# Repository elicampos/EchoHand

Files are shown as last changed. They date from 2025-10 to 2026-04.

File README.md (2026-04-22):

# EchoHand

A haptic feedback glove for VR applications utilizing ESP32-S3 microcontrollers. 

## Project Overview

EchoHand is a wearable haptic glove that captures hand and finger movements, and provides haptic feedback through the servo motors. The system communicates primary through WI-FI but also supports USB and Bluetooth Serial to transmit all the sensor data to the computer in real-time through the OpenGloves application.

## System Architecture

### External Interface

The external interface layer is executed primarily in `SerialCommunication.cpp` or `WifiCommuncation.cpp` and is responsible for receving and sending packets to the computer running the virtual reality enviornment.

- Configures Bluetooth Serial Communcation and has some variables to toggle AT mode for baudrates changes
- Configures ESP-NOW which allows the ESP32-S3 to talk to the computer quickly and asynchronously.
- Configures USB Serial by printing through default COM port

### DataBroker

Data storage is managed through `DataBroker.h`, which implements a singleton pattern for centralized state management. This component:

- Provides getters and setters for all sensor and actuator values
- Implements a snapshot mechanism with revision counters for consistent multi-field reads
- Stores current values for finger angles, servo positions, and button inputs

### Internal Systems

The internal processing layer handles data transformation and control logic. This component performs:

- **Sensor Mapping**: Get's center of raw ADC values (0-4095) to get more accurate values
- **Command Translation**: Translates serial commands PWM signals for servo motor control
- **State Updates**: Continuously updates the DataBroker with processed sensor data
- **Haptic Control**: Manages the relationship between virtual interactions and physical feedback through servo systems

### Information Handling

Data integrity is maintained through:
- Validation of sensor data ranges before processing
- Error checking on state updates to prevent corruption
- Verifying presence of the null terminator character in strings to prevent overflows
- Ensuring we never read outside of the bounds of C-style strings

### Communication

Communication is done through WI-FI, USB Serial, Bluetooth Serial and is dependent on the values in `config.h`.
- **Output Characteristic**: Transmits finger angle data and button values
- **Input Characteristic**: Receives haptic feedback commands for servos

### Integrity & Resilience

Current security and reliability features include:
- **RTOS Task Management**: FreeRTOS ensures deterministic behavior 

Future security and reliability features include:
- **Encryption**: All Bluetooth packets are encrypted(after pairing) to prevent man-in-the-middle attacks
- **Pairing Protocol**: Only authenticated devices can connect and exchange data

## Known Bugs

### 1. Random Finger position Jitter
**Description**: Due to no low-pass filter on the slider pins. Implementing this via software will cause too much of a delay.

## Future Work

#### 1. User-facing application for easy firmware changes
- **Description**: Create GUI software to allow users to send custom or pre-configured payloads to the EchoHand to update the current EchoHand settings during run-time.

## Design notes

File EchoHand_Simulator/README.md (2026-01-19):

# EchoHand Simulation Guide

## 1. Environment Setup

Make sure you are running this on a windows machine as this is a windows only application.

### ESP-IDF Extension (VSCode)
1.  **Install the Extension**: Search for "ESP-IDF" in the VSCode Extensions marketplace and install it.
2.  **Setup / Configuration**:
    *   Open the setup wizard (Command Palette: `ESP-IDF: Configure ESP-IDF extension`).
    *   **CRITICAL**: Select version **v5.3.4**. This version is strictly required for compatibility with the Arduino library used in this project.
    *   Follow the prompts to install tools.
3.  **Target Selection**:
    *   Set the target device to **esp32s3**.
    *   (Command Palette: `ESP-IDF: Set Espressif Device Target` -> `esp32s3`).

### Wokwi Simulator Extension (VSCode)
1.  **Install the Extension**: Search for "Wokwi for VSCode".
2.  **License**: You will need a valid license. Follow the extension's prompts to get a license from the Wokwi website and activate it.

---

## 2. Running the Firmware Simulation

1.  **Build Firmware**:
    *   Use the ESP-IDF extension icons (usually at the bottom bar) or Command Palette `ESP-IDF: Build your project` to compile the firmware.
2.  **Start Simulation**:
    *   Open the `diagram.json` file (or open the Wokwi GUI).
    *   Start the simulation.
    *   **Note**: The Wokwi simulation acts as the TCP Server. It must be running *before* you start the desktop visualizer.

> [!IMPORTANT]
> **Focus Issue**: If the data stream from Wokwi stops or lags, make sure you **click back into the VSCode window** showing the simulation. Browsers/Electron apps sometimes throttle background tabs/windows.

---

## 3. Running the Desktop Simulator

The desktop application visualizes the hand data received from the Wokwi simulation.

1.  **Navigate to Directory**:
    Open a terminal and navigate to the simulator folder:
    ```powershell
    cd EchoHand_Simulator
    ```

2.  **Build Application**:
    Run `make` to compile the C++ application (ensure you have MinGW/Make installed):
    ```powershell
    make
    ```

3.  **Run Application**:
    Execute the binary from the `bin` folder:
    ```powershell
    .\bin\opengloves_sim.exe
    ```

---

## 4. Controls & Interaction

Once both the Simulation (Server) and Desktop App (Client) are running:

*   **Modify Payload**:
    *   **Potentiometers**: Adjust these in the Wokwi view to simulate **Flex Sensors** (controlling finger curl).
    *   **Buttons**: Click to simulate Controller Buttons (A, B, Trigger, etc.).
    *   **Joystick**: Drag to simulate joystick movement.

*   **Desktop App Controls**:
    *   `W`, `A`, `S`, `D`: Move Camera
    *   `Right Click + Drag`: Look Around
    *   `P`: Toggle Protocol Reference Overlay

---

## Important Notes

*   **Launch Order**: ALWAYS run the **Wokwi Simulation first**, then the **OpenGloves Simulator**. The simulator tries to connect to localhost on launch; if the server isn't there, it will fail.
*   **Missing Payloads**: If you don't see the hand moving, check that Wokwi is actually sending data (monitor the serial output in VSCode) and that the VSCode window is focused.
*   **Future Features**: 
    *   Support for servo feedback (computer -> esp32).
    *   Reading commands from the computer.

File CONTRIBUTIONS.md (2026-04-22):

Name | Date | Start Time | End Time | Total Time (HH:MM) | Description of Work
--- | --- | --- | --- | --- | --- 
Anton Rushevich, Eli Campos, Gabriella Conde, Michael Knauf, Shawn Rhoads | 10/01/2025 | 12:00:00 PM | 12:00:00 PM | 0:00:00 | Work on Design Draft document. 
Eli Campos | 10/02/2025 | 99:99 PM | 99:99 PM | 0:00 | Work on Draft Schematic.
Eli Campos | 10/03/2025 | 99:99 PM | 99:99 PM | 0:00 | Work on Draft Schematic and High-Level System Diagram.
Eli Campos | 10/11/2025 | 99:99 PM | 99:99 PM | 0:00 | Work on sourcing and ordering parts.
Michael Knauf | 10/15/2025 | 7:27 PM | 8:09 PM | 0:40 | Work on Environmental Sustainability section for Design Plan revision, revising time sheet
Gabriella Conde | 10/18/2025 | 5:16 AM | 6:24 AM | 01:08 | Research and write repairability section of Design Draft.
Eli Campos | 10/19/2025 | 12:00 AM | 4:17 AM | 4:17 | Research and write risk section of Design Draft. 
Michael Knauf | 10/25/2025 | 8:05 PM | 10:00 PM | 1:55 | Set up Arduino environment and tested and showed that Bluetooth Serial failed
Eli Campos | 10/25/2025 | 12:30 PM | 6:00pm | 5:30 | Reading ESP32 Docuementation on the adc and pushed first RTOS main file.
Michael Knauf | 10/25/2025 | 1:12 PM | 10:15 PM | 9:03 | Making BLE Pre-alpha setup and debugging BLE integration
Gabriella Conde | 10/25/2025 | 2:36 PM | 6:25 PM | 3:49 | Drafting and prototyping of flex-sensor/esp32 circuit.
Shawn Rhoads | 10/26/2025 | 11:38 AM | 5:32 PM | 5:56 | Initial data store code and BLE integration
Eli Campos | 10/26/2025 | 3:00 PM | 12:00 AM | 9:00 | Finializing adc polling code, tweaking circuit and purchasing more components. 
Shawn Rhoads | 10/26/2025 | 9:00 PM | 11:59 PM | 2:59 | Fixing data store / BLE issues, coordinating team coding efforts 
Gabriella Conde | 10/26/2025 | 4:01 PM | 5:27 PM | 1:26 | Began expanding flex-sensor/esp32 circuit to incorporate joysticks, buttons, and servo motors.
Anton Rushevich | 10/26/2025 | 4:23 PM | 11:35 PM | 07:12 | Implemented InternalSystem.cpp to handle serial communication with the ESP32, sending simulated data and receiving state snapshots for testing internal system functionality.
Eli Campos | 11/02/2025 | 4:00 PM | 10:00 PM | 6:00 | Source tools and parts for prototype. Begin basic assembly. 
Gabriella Conde | 11/03/2025 | 2:43 AM | 3:52 AM | 1:09 | Assemble haptic spool prototype.
Shawn Rhoads | 11/03/2025 | 1:00 PM | 5:00 PM | 3:00 | Test VR Headset in Custom Unity Environment
Michael Knauf | 11/04/2025 | 5:05 PM | 7:00 | 1:55 | code connection to Bluetooth serial periferal through UART
Gabriella Conde | 11/04/2025 | 1:28 AM | 2:04 AM | 0:36 | Prepare 3-D printed parts for assembly.
Michael Knauf, Eli Campos | 11/05/2025 | 5:20 AM | 6:05 PM | 0:45 | working on debugging Bluetooth Serial Module
Michael Knauf | 11/05/2025 | 6:22 PM | 6:56 PM | 0:34 | working on getting BthS working with ESP32
Michael Knauf | 11/10/2025 | 6:48 PM | 7:02 PM | 0:14 | Changing main to use Bluetooth Serial
Eli Campos | 11/12/2025 | 6:00 PM | 11:00 PM | 5:00 | Source additonal parts and set up haptic spools
Gabriella Conde | 11/12/2025 | 5:16 AM | 7:20 AM | 2:04 | Assemble haptic spools.
Eli Campos | 11/13/2025 | 6:00 PM | 9:00 PM  | 3:00 | Wire ESP32 to parts.
Shawn Rhoads | 11/13/2025 | 4:03 PM | 4:48 PM | 00:45 | Customize unity environment
Eli Campos | 11/14/2025 | 12:30 AM | 6:53 AM  | 6:23 | Add joystick, buttons and servos to microcontroller code.
Gabriella Conde | 11/14/2025 | 1:28 AM | 6:59 AM | 5:31 | Fix broken spool, assemble prototype wires and gloves
Eli Campos | 11/16/2025 | 3:50 PM | 12:00 AM | 8:10 | Add openhaptics support
Shawn Rhoads | 11/15/2025 | 10:30 AM | 12:00 PM | 1:30 | Working on integrating Unity with the physical glove
Michael Knauf, Eli Campos | 4:49 | 6:49 | 2:00 | Switching Bluetooth to Serial for prototype.
Shawn Rhoads | 11/16/2025 | 2:35 PM | 9:52 PM | 7:17 | Testing glove interaction in VR environment, fixing serial code with Eli
Gabriella Conde | 11/27/2025 | 11:39 PM | 12:19 AM | 0:40 | Debug flex sensors
Eli Campos | 11/27/2025 | 6:00 PM | 12:19 AM | 6:19 | Debug flex sensors
Eli Campos | 11/30/2025 | 10:00 PM | 12:54 AM | 2:54 | Noise filtering done through circuit now 
Eli Campos | 12/2/2025 | 1:00 AM | 4:39 AM | 4:39 | Add more stable configuration through code and re-do tape attachments for demo
Eli Campos | 12/29/2025 | 12:00 AM | 6:00 AM | 6:00 | Migrating to ESP-IDF instead of only using Ardunio to get access to more stuff on esp32
Eli Campos | 12/30/2025 | 1:00 AM | 5:00 AM | 4:00 | Writing socket and serial driver to parse through opengloves
Eli Campos | 12/31/2025 | 1:00 AM | 5:20 AM | 4:20 | Creating 3d enviornment simulation of glove flexing based off simulated circuit data from Wokwi
Eli Campos | 1/17/2026 | 12:00 AM | 6:00 AM | 6:00 | Rebuilding Circuit to accomdate bluetooth serial and refactoring code
Eli Campos | 1/17/2026 | 11:00 AM | 5:00 AM | 6:00 | Getting bluetooth to finally work and adding config option for either serial or bluetooth
Eli Campos | 1/21/2026 | 2:00 AM | 6:00 AM | 4:00 | Modified code to poll the adc more accurately and added a calibration phase
Eli Campos | 1/22/2026 | 1:00 AM | 3:00 AM | 3:00 | Modified circuit to use insulated wires to help reduce noise 
Gabriella Conde| 1/22/2026 | 1:00 AM | 6:25 AM | 5:25 | Assembled haptic spool system onto left glove
Eli Campos | 1/22/2026 | 3:00 AM | 7:00 AM | 4:00 | Modified circuit to read potentiometers as finger positions
Eli Campos | 1/26/2026 | 11:00 PM | 7:40 AM | 8:40 | Added new buttons, resembled haptic spools and added servos
Gabriella Conde | 1/26/26 | 11:00 PM | 7:44 AM | 8:44 | Crimped wires
Michael Knauf | 1/29/26 | 12:03 PM | 12:59 PM | 0:56 | Start Installing and Learning CAD
Michael Knauf | 1/29/26 | 6:19 PM | 11:46 PM | 5:27 | Starting CAD design, made initial design for joystick holder
Michael Knauf | 1/30/26 | 12:20 AM | 6:00 AM | 5:40 | Starting initial design for button holder
Gabriella Conde | 1/30/206| 4:40 AM | 7:15 AM | 2:35 | Worked on Aplaj Bukd and Alpha Test documents.
Eli Campos | 1/30/26 | 4:00 AM | 7:20 AM | 3:20 | Finalize haptic spool circuit.
Michael Knauf | 1/30/26 | 6:20 AM | 12:04 AM | 5:44 | finished first iteration of button holder
Shawn Rhoads | 1/30/26 | 1:48 PM | 7:57 PM | 6:09 | Building and running the simulator and ESP IDF, debugging the Joystick issue
Gabriella Conde | 1/30/26 | 10:00 PM | 11:30 | 1:30 | Work on Alpha Build and Alpha Test documents.
Eli Campos | 1/30/26 | 8:30 PM | 11:30 | 3:00 | Work on Alpha Build and Alpha Test documents.
Michael Knauf | 1/31/26 | 2:08 PM | 6:28 PM | 4:20 | Adjusting and reprinting current button rig design
Eli Campos | 2/3/26 | 12:00 AM | 2:30AM | 2:30 | Update RTOS scheme, refactor code for more user set defintions and fix slight bugs
Gabriella Conde | 2/3/26 | 3:00 AM | 4:30 AM | 1:30 | Secure servo motors in place. Re-glue finger cap.
Michael Knauf | 2/6/2026 | 12:57 PM | 4:07 | 3:10 | First iteration of new Joystick rig w/o straps.
Eli Campos | 2/11/26 | 10:00 PM | 12:00AM | 1:00 | Take apart Alpha build, place on prototype board for upcoming soldering. 
Michael Knauf | 2/14/2026 | 5:00 PM | 7:00 PM | 2:00 | Printing and prototyping joystick casing
Gabriella Conde | 2/17/26 | 4:00 PM | 7:00 PM | 3:00 | Solder protoboard.
Gabriella Conde | 2/18/26 | 10 PM | 5 AM | 7 | Learn FreeCAD, design circuit casing, 3D printing.
Gabriella Conde | 2/18 | 5 PM | 7P | 2 | solder protoboard 
Gabriella Conde | 2/20 | 12 am | 5 am | 5:00 | Casing design
Gabriella Conde| 2/20 | 4 pm | 6 pm | 2:00 | Solder protoboard 
Shawn Rhoads | 2/21/26 | 10:00 PM | 6:00 AM | Test gloves on personal computer, try to set up communication
Shawn Rhoads | 2/22/26 | 6:00 PM | 9:00 PM | Attempts to get the glove to work on the computer; cant connect
Eli Campos | 2/21/26 | 4:00 PM | 2:00 AM | 10:00 | Fix Simulation, Test Soldered Circuit and Fix Task Priority Bug
Eli Campos | 2/23/26 | 2:00 PM | 3:20 AM | 1:20 | Decrease servo action delay
Eli Campos | 3/1/26  | 2:00 AM | 9:25 AM | 7:25 | Fix shorted circuit from Beta
Eli Campos | 3/2/26  | 7:30 PM | 8:20 PM | 0:50 | Add new working bluetooth module
Eli Campos | 3/3/26  | 3:00 AM | 7:00 AM | 5:00 | Debugging random pinkie jitters
Eli Campos | 3/3/26  | 8:00 PM | 12:00 AM | 4:00 | Creating Unity Enviornment for custom grabbing 
Eli Campos | 3/4/26  | 4:00 AM | 6:00 AM | 2:00 | Finish Unity Enviornment for custom grabbing and change calibration algorithm
Michael Knauf | 3/5/26 | 2:06 PM | 8:09 | 6:00 | adjusting holes to fit screws for joystick rig and added prototype holes for straps
Gabriella Conde | 3/ 13/26 | 11:30 am | 1:30 PM | 2:00 | pcb
Shawn Rhoads | 3/15/26 | 3:00 PM | 6:00 PM | 3:00 | Testing haptic delay, looking for possible improvements on speed
Shawn Rhoads | 3/16/26 | 6:00 PM | 7:30 PM | 1:30 | Trying to change timeout rate, program no longer working
Shawn Rhoads | 3/19/26 | 5:00 PM | 10:00 PM | 5:00 | Trying to get the program to work, reverting to original code, trying hardware fixes
Shawn Rhoads | 3/24/26 | 7:50 PM | 12:00 AM | 4:10 | Workin with Eli to find why it wont work on my PC, identifying causes of delay
Eli Campos | 3/31/26 | 9:00 PM | 4:51 AM  | 7:51 | Created new haptic guide module, resoldering everything for ADC1 and getting ready for wifi-integration
Gabriella Conde | 4/1/26 | 2:00 AM | 2:50 AM | 0:50 | Crimped a header JST pin for new circuit
Eli Campos | 4/1/26 | 5:00 AM | 6:21 AM  | 1:21 | Wrote ESP-NOW master code
Eli Campos | 4/6/26 | 12:00 AM | 3:00 AM  | 3:00 | Wrote ESP-NOW slave code
Gabriella Conde | 4/20/26 | 1 AM | 7 AM | 6:00 | new case
Gabriella Conde | 4/20/26 | 8 PM | 7 AM | 11:00 | Fix case dimensions, 3D print parts, add straps
Michael Knauf | 4/3/26 | 5:00 PM | 12 AM | 7:00 | redesign joystick, adding in loop for strap that actually works
Michael Knauf | 4/4/26 | 8:20 PM | 11:29 PM | 2:51 | reprint new joystick design
Michael Knauf | 4/7/26 | 12:44 AM | 5 AM | 4:16 | redesigning and reprinting button rigor with strap

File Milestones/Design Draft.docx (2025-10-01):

### Introduction

Purpose / Need: (grab from video/presentation from Eli)

Domain & Prior Art: (grab from video/presentation from Eli, sources from the internet)

Impact & Risk Assessment:

### Statement of Work

Check announcements forum for team selection: list out responsibilities

### Deliverable Artifacts

See above

# Mockups

### Interfaces

- OpenVR API

### Systems

### Networking

-wired serial initially, then Bluetooth for wireless

### Storyboards

### Draft Schematics

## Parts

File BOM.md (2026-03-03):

Date | Name | Item | Price
--- | --- | --- | ---
10/06/2025 | Eli Campos | 3x ESP32-C | $16.99
10/11/2025 | Eli Campos | 5x Flex Sensor | $48.47
10/27/2025 | Eli Campos | 10x Vibration Motors , x50 Badge Reels, x1 Crimping Tool kit, x10 Potentiometers | $78.39
10/29/2025 | Eli Campos | 3-D printing parts for prototype | $18.12
1/15/2025 | Eli Campos | 3-D printing end caps for prototype | ~$4
11/13/2025 | Eli Campos | Gloves from Harbor Freight | $~6
11/16/2025 | Eli Campos | Flex Sensor Secure Clamps | $11.09
03/01/2026 | Gabriella Conde | Bluetooth module | $10.74

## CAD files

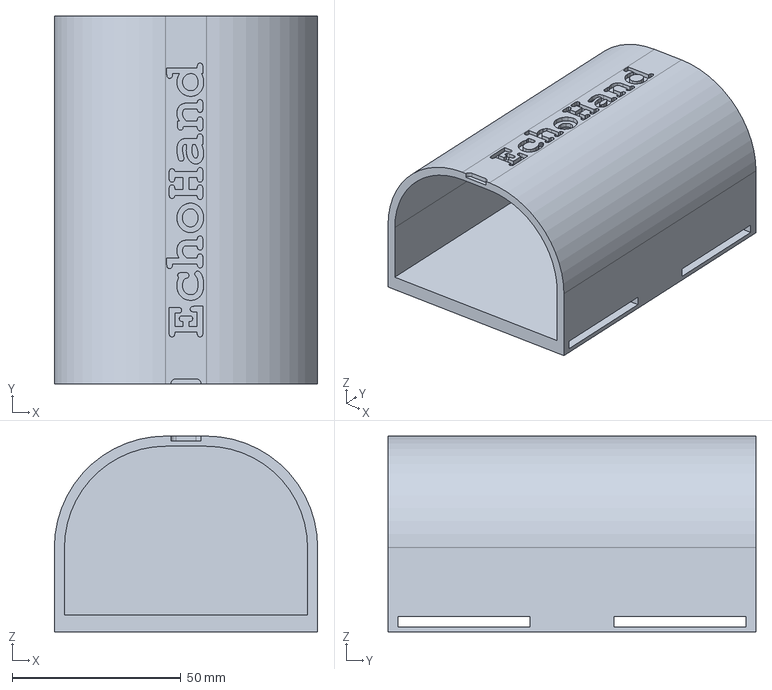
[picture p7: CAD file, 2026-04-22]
CAD/EchoHand_circuit_case_v4.FCStd
78.0 x 109.0 x 58.0 mm

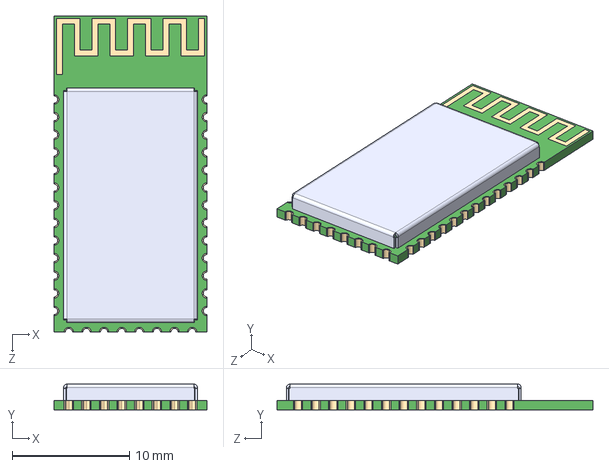
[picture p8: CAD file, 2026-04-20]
Schematics/EchoHand_v2/HC-05/HC-05.step
13.0 x 2.20 x 26.9 mm

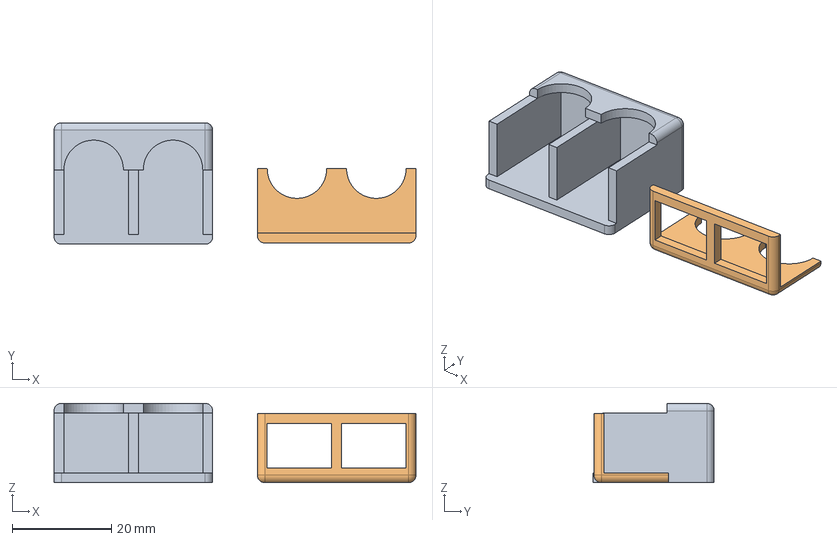
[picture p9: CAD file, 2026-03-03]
CAD/Button rig 3.step
73.0 x 24.5 x 16.0 mm

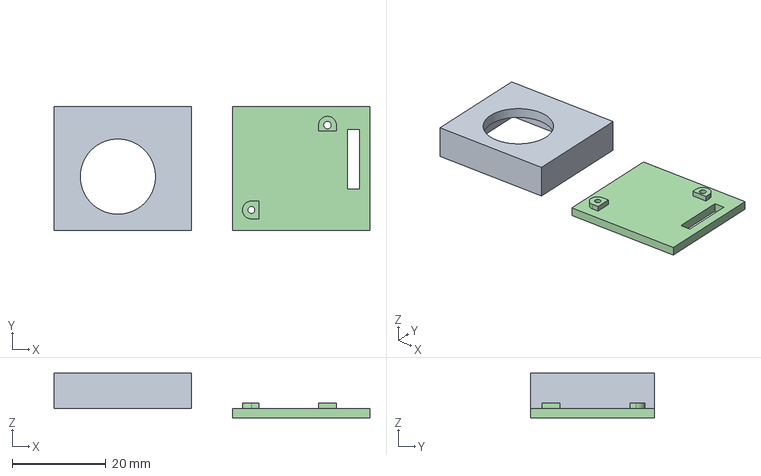
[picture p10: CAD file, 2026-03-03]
CAD/Joystick Rig pt3_.step
67.2 x 26.4 x 9.50 mm

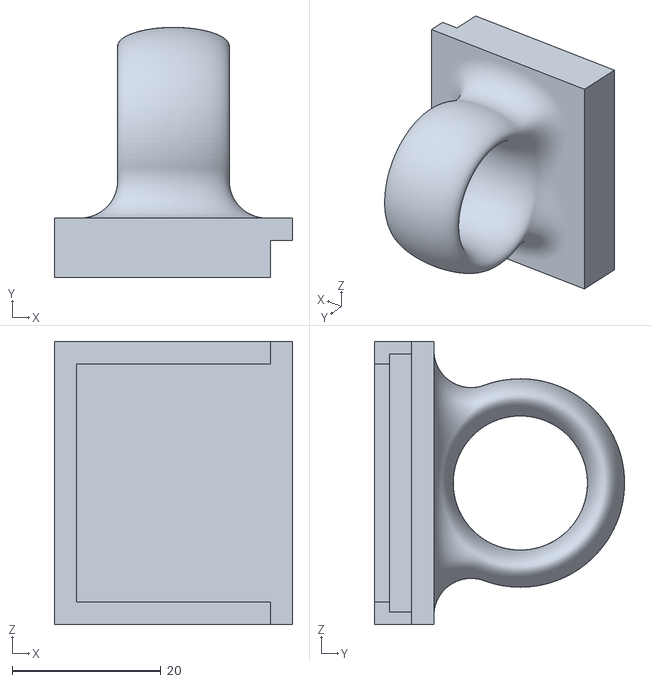
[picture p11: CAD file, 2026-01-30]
CAD/JoystickRingM1.stl
32.0 x 33.6 x 38.0

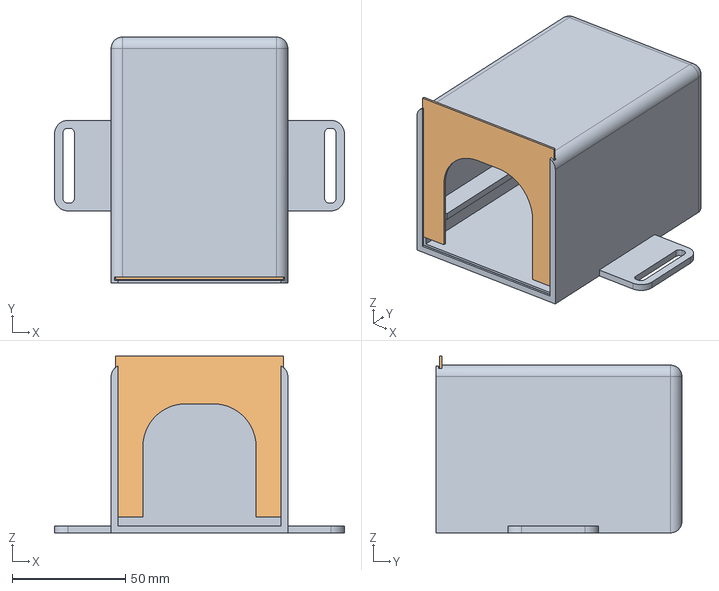
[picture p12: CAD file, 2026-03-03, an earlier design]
CAD/EchoHand_circuit_case_v3.FCStd
128.0 x 108.5 x 78.0 mm
Case
Lid

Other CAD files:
CAD/Button Ring2.f3d
CAD/Button rig 3.f3d
CAD/Button rig 3.stl
CAD/Joystick Rig pt3_.f3d
CAD/Joystick Rig pt3_.stl
CAD/Joystick Rig pt4_.f3d
CAD/JoystickRingM1.f3d

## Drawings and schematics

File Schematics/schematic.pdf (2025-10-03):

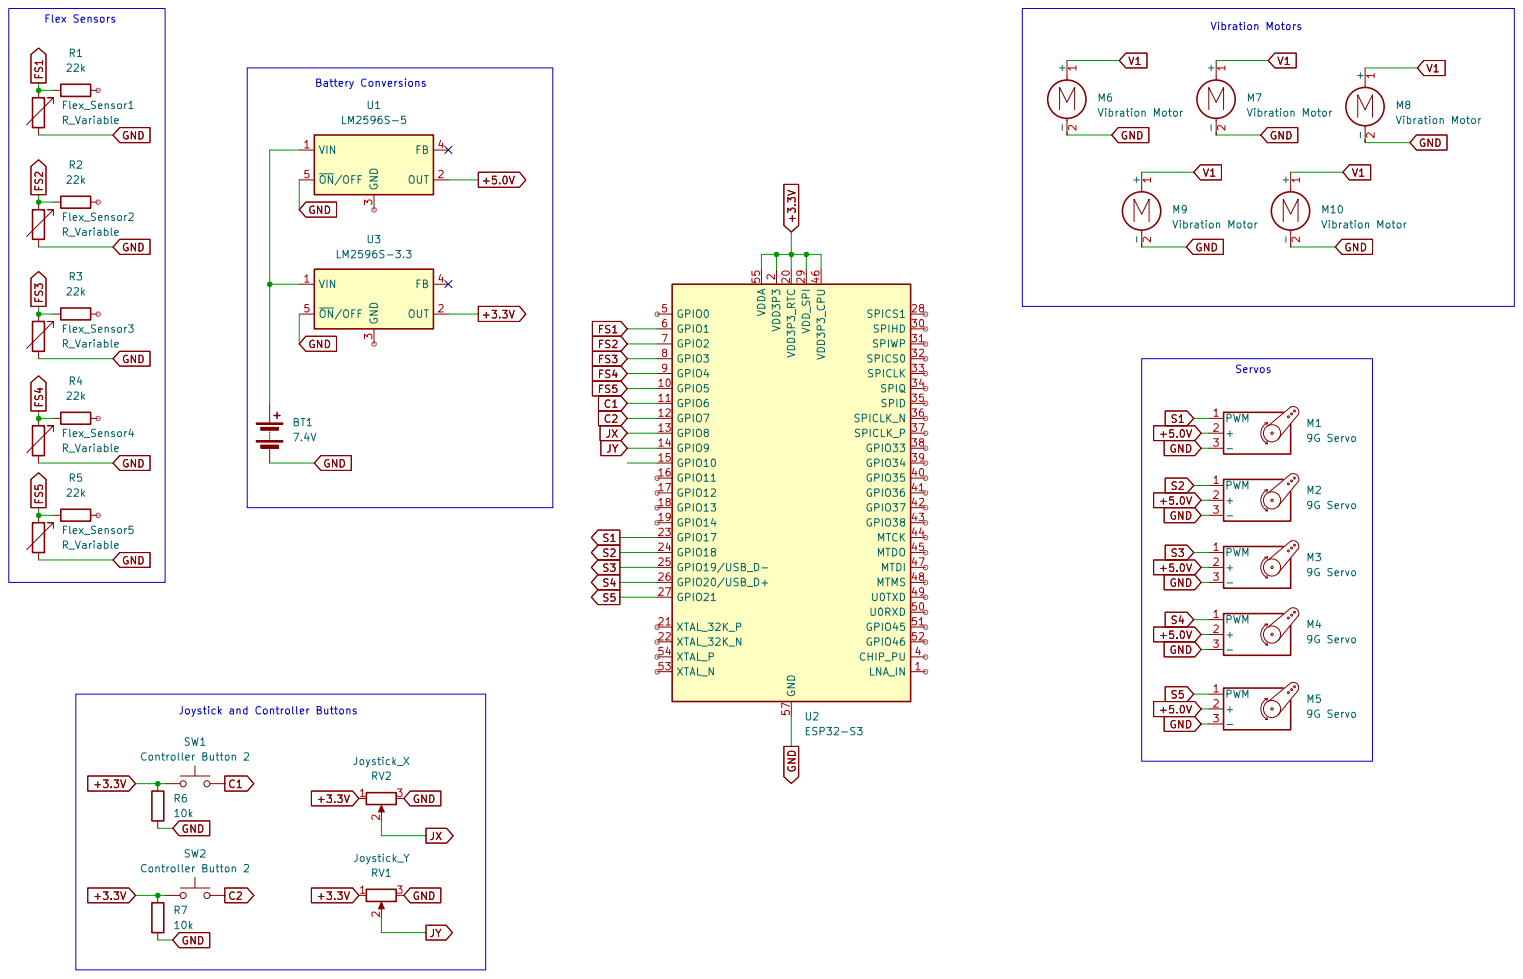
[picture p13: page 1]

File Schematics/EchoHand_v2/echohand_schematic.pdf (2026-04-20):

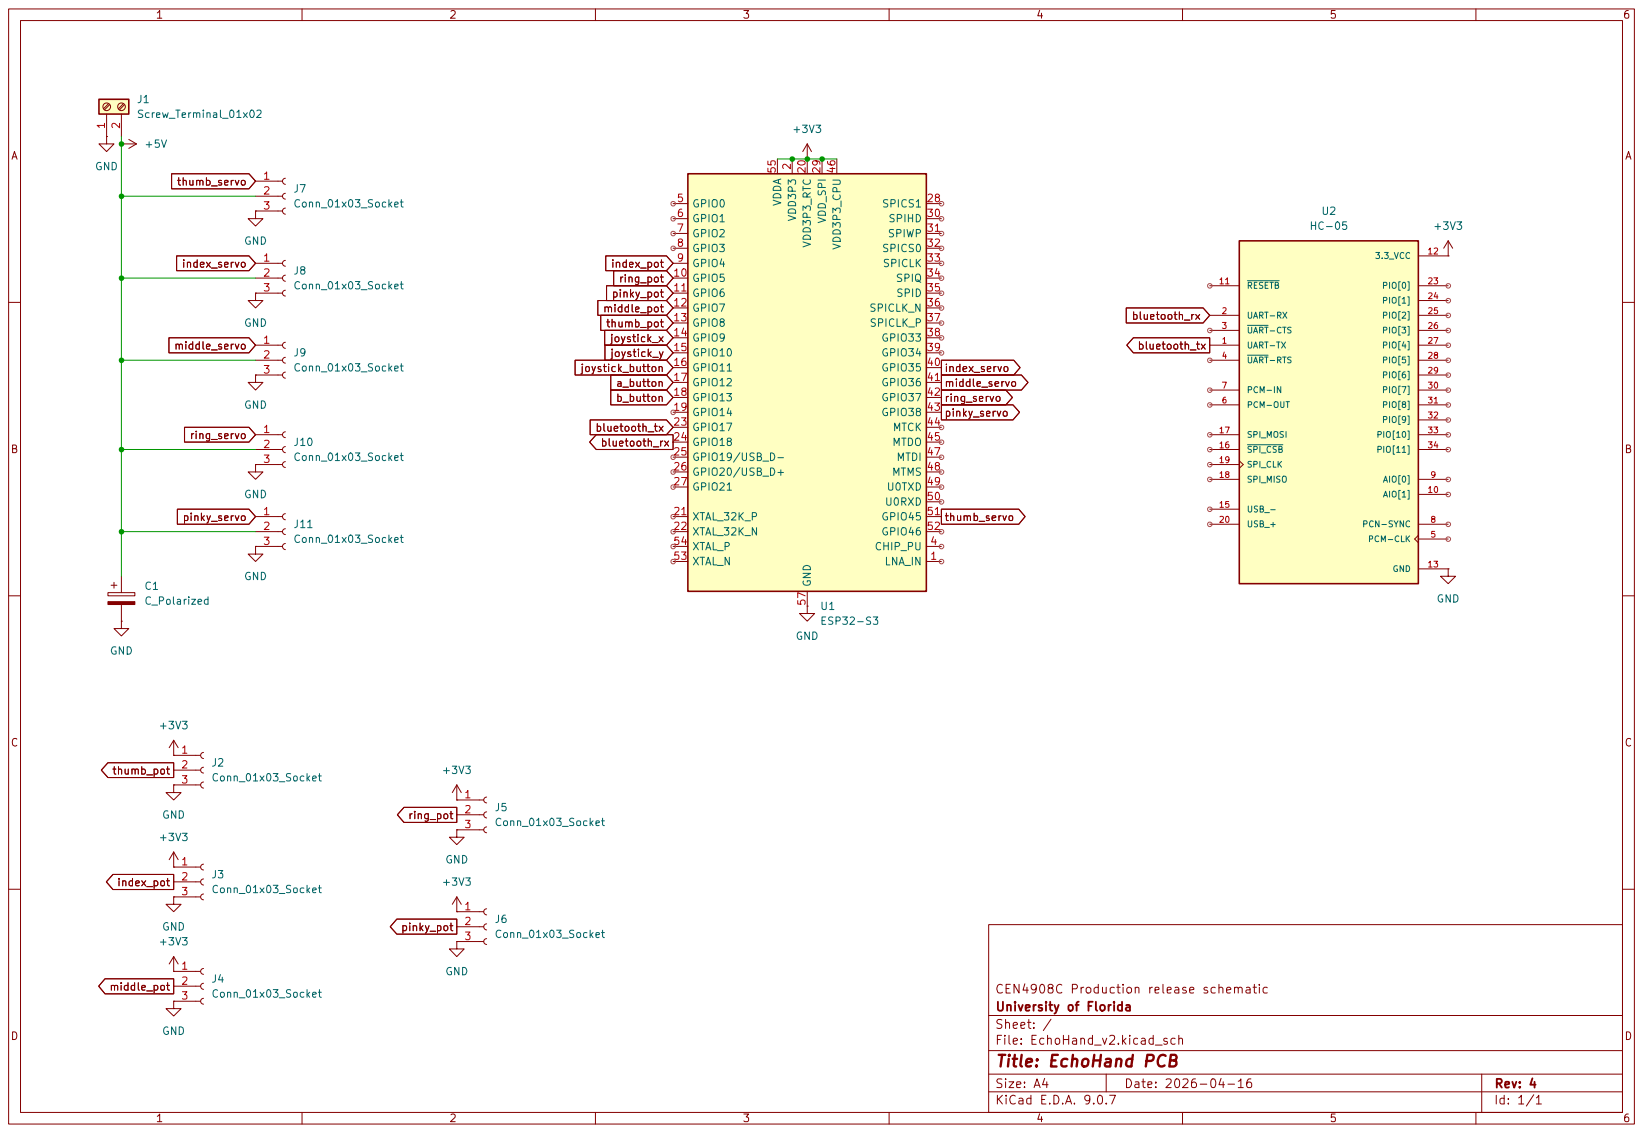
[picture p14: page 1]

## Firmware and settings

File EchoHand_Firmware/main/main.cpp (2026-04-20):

#include "freertos/FreeRTOS.h"
#include "freertos/task.h"
#include "config.h"
#include "DataBroker.h"
#include <ESP32Servo.h>
#include <WiFi.h>
#include <Arduino.h>

// Import all tasks
#include "AnalogRead_task.h"
#include "SerialCommunication_task.h"
#include "DataBrokerPrint_task.h"
#include "ServoControl_task.h"
#include "WifiCommuncation.h"

// Allocate memory for servo task handler
TaskHandle_t xServoTaskHandle = NULL;

void setup()
{
    // Set BaudRate
    Serial.begin(115200);

    // Debug Print
    Serial.println("Starting FreeRTOS Setup...");

    if (DEBUG_PRINT)
    {
        xTaskCreatePinnedToCore(
            TaskDataBrokerPrint, // Fucntion name of Task
            "DataBrokerPrint",   // Name of Task
            8192,                // Stack size (bytes) for task
            NULL,                // Parameters(none)
            0,                   // Priority level(0->Lowest)
            NULL,                // Task handle(for RTOS API maniuplation)
            0                    // Run on core 0
        );
    }

    // Create the task
    xTaskCreatePinnedToCore(
        TaskAnalogRead, // Fucntion name of Task
        "AnalogRead",   // Name of Task
        8192,           // Stack size (bytes) for task
        NULL,           // Parameters(none)
        0,              // Priority level(0->lowest)
        NULL,           // Task handle(for RTOS API maniuplation)
        1               // Run on core 1
    );

    if (COMMUNCATION <= 1)
    {
        xTaskCreatePinnedToCore(
            TaskSerialCommunication, // Fucntion name of Task
            "SerialCommunication",   // Name of Task
            8192,                    // Stack size (bytes) for task
            NULL,                    // Parameters(none)
            0,                       // Priority level(1->highest)
            NULL,                    // Task handle(for RTOS API maniuplation)
            0                        // Run on core 0
        );
    }
    else
    {
        xTaskCreatePinnedToCore(
            TaskWifiCommunication, // Fucntion name of Task
            "WifiCommunication",   // Name of Task
            8192,                  // Stack size (bytes) for task
            NULL,                  // Parameters(none)
            0,                     // Priority level(1->highest)
            NULL,                  // Task handle(for RTOS API maniuplation)
            0                      // Run on core 0
        );
    }

    xTaskCreatePinnedToCore(
        TaskServoControl,  // Fucntion name of Task
        "ServoControl",    // Name of Task
        8192,              // Stack size (bytes) for task
        NULL,              // Parameters(none)
        1,                 // Priority level(1->highest)
        &xServoTaskHandle, // Task handle(for RTOS API maniuplation)
        1                  // Run on core 1
    );
}

extern "C" void app_main()
{
    // Initialize the Arduino framework
    initArduino();

    // Call the standard setup
    setup();

    // Delete task so that we don't hog any cpu time
    vTaskDelete(NULL);
}

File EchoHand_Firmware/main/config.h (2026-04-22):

#pragma once

// Stops outputting in openglove format and outputs the persistant state values read
#define DEBUG_PRINT 0

// Serial Plot values instead of having a readable format
#define USE_SERIAL_PLOTTER 0

// Use for setting UP AT commands on external bluetooth device
#define BLUETOOTH_SETUP 0

// Setup communcation method
// 0->Wired over Serial
// 1->Bluetooth Serial
// 2-> WIFI (ESPNOW)
// Enable WIFI mode(note bluetooth serial must be set to 0)
#define COMMUNCATION 2

// Averages values read from flex sensor by x amount
#define POT_SAMPLE_RATE 16

// Enable which noise reducation algo for flex sensor adc polling
// 0-> No average
// 1-> Average
// 2-> Median
// 3->Trimmed Mean
#define POLL_METHOD 2

// Calibration Phase Method
// 0 -> Average
// 1-> Most extreme value
#define CALIBRATION_METHOD 1

// If running Wokawai Simulation
#define SIMULATION 0

// Servo deadzone used for haptics
#define SERVO_DEADZONE 0

// Pot enabled
#define JOYSTICK_ENABLE 0

//-------Circuit Pin Connections-------//

// Potentiometers
inline constexpr uint8_t THUMB_POT = 8;
inline constexpr uint8_t INDEX_POT = 4;
inline constexpr uint8_t MIDDLE_POT = 7;
inline constexpr uint8_t RING_POT = 5;
inline constexpr uint8_t PINKIE_POT = 6;

// Servos
inline constexpr uint8_t THUMB_SERVO = 45;
inline constexpr uint8_t INDEX_SERVO = 35;
inline constexpr uint8_t MIDDLE_SERVO = 36;
inline constexpr uint8_t RING_SERVO = 37;
inline constexpr uint8_t PINKIE_SERVO = 38;

// Joystick and buttons
inline constexpr uint8_t JOYSTICK_BUTTON = 11;
inline constexpr uint8_t JOYSTICK_X = 9;
inline constexpr uint8_t JOYSTICK_Y = 10;
inline constexpr uint8_t A_BUTTON = 12;
inline constexpr uint8_t B_BUTTON = 15;

// Bluetooth Buttons
inline constexpr uint8_t BLUETOOTH_RX = 18;
inline constexpr uint8_t BLUETOOTH_TX = 17;

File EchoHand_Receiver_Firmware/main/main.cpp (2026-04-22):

#include <cstring>
#include <cstdio>
#include <math.h>
#include <string>
#include <WiFi.h>
#include <esp_now.h>
#include "Arduino.h"

// Global to copy analog data
char analog_data[56];

// Is there valid data
volatile bool new_data = false;

// Global for received data(finger angles, buttons and etc)
void on_data_receive(const esp_now_recv_info_t *esp_now_info, const uint8_t *incoming_data, int len)
{
  // Prevent buffer overflow and ensure null-termination
  int copy_len = len < 55 ? len : 55;

  // Copy into output string
  memcpy(analog_data, incoming_data, copy_len);

  // Ensure null-terminator
  analog_data[copy_len] = '\0';

  // Print valid data
  new_data = true;
}

extern "C" void app_main()
{
  // Initalize Arduino
  initArduino();

  Serial.begin(115200);

  // Info of other ESP32 connected to PC
  esp_now_peer_info_t peerInfo;

  // Global array for servo angles
  uint8_t servoTargetAngles[5];

  // MAC address of other ESP32
  uint8_t broadcastAddress[] = {0x80, 0xB5, 0x4E, 0xC3, 0x20, 0x2C};

  // Setup ESP32 WIFI Moudle
  WiFi.mode(WIFI_STA);

  // Check if it initalized
  while (esp_now_init() != ESP_OK)
  {
    Serial.println("Error setting up ESP_NOW");
  }

  // Print ESP32 MAC Address
  Serial.print("ESP32 MAC Address: ");
  Serial.println(WiFi.macAddress());

  // Clear struct
  memset(&peerInfo, 0, sizeof(peerInfo));

  // Register Peer
  memcpy(peerInfo.peer_addr, broadcastAddress, sizeof(broadcastAddress));
  peerInfo.channel = 0;
  peerInfo.encrypt = false;

  // Set Wi-FI interface to station mode
  peerInfo.ifidx = WIFI_IF_STA;

  while (esp_now_add_peer(&peerInfo) != ESP_OK)
  {
    Serial.println("Failed to add peer MAC Address.");
  }

  // Register callback for data received
  esp_now_register_recv_cb(on_data_receive);

  // String for Servo payload
  char output_string[256];

  for (;;)
  {
    // Check if we got a servo packet
    // If we have data available to read, parse it and update servo targets
    if (Serial.available() > 10)
    {
      // Use readBytesUntil to safely read a full line into the buffer with a timeout, unlike with just using read
      size_t len = Serial.readBytesUntil('\n', output_string, sizeof(output_string) - 1);

      // make sure last char is null terminator
      output_string[len] = '\0';

      // Send the constructed string as one STRING(+ null terminator)
      // len+1 since arrays are 0 indexed
      esp_now_send(broadcastAddress, (uint8_t *)output_string, len + 1);
    }

    if (new_data == true)
    {
      // Write until size of analog data(56 bytes) or null terminator met
      Serial.write(analog_data, strlen(analog_data));

      // Mark data as old
      new_data = false;
    }

    vTaskDelay(1);
  }
}

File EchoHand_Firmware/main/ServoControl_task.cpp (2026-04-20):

#include "ServoControl_task.h"

// Description: Commands all haptic spools
// Parameters: pvParameters which is a place holder for any pointer to any type
// Return: none, it will simply pass the information on to the next core for processing
void TaskServoControl(void *pvParameters)
{

    // Set pin modes
    pinMode(THUMB_SERVO, OUTPUT);
    pinMode(INDEX_SERVO, OUTPUT);
    pinMode(MIDDLE_SERVO, OUTPUT);
    pinMode(RING_SERVO, OUTPUT);
    pinMode(PINKIE_SERVO, OUTPUT);

    // Setup servo objects
    Servo thumbServo;
    Servo indexServo;
    Servo middleServo;
    Servo ringServo;
    Servo pinkieServo;

    thumbServo.attach(THUMB_SERVO);
    indexServo.attach(INDEX_SERVO);
    middleServo.attach(MIDDLE_SERVO);
    ringServo.attach(RING_SERVO);
    pinkieServo.attach(PINKIE_SERVO);

    // To not get compiler unused variable error
    (void)pvParameters;

    // Reset all servo angles to 0 so user can use glove
    // Get servo angle from openhaptics
    thumbServo.write(180);
    indexServo.write(180);
    middleServo.write(180);
    ringServo.write(180);
    pinkieServo.write(180);

    // Fetch analog data from sensors forever
    for (;;)
    {
        // Wait until all servo values have been updates from the communcation task
        ulTaskNotifyTake(pdTRUE, portMAX_DELAY);

        // Get servo angle from openhaptics
        int thumbAngle = DataBroker::instance().getServoTargetAngle(0);
        int indexAngle = DataBroker::instance().getServoTargetAngle(1);
        int middleAngle = DataBroker::instance().getServoTargetAngle(2);
        int ringAngle = DataBroker::instance().getServoTargetAngle(3);
        int pinkieAngle = DataBroker::instance().getServoTargetAngle(4);

        /*
        if (thumbAngle <= SERVO_DEADZONE)
        {
            thumbAngle = 0;
        }
        if (indexAngle <= SERVO_DEADZONE)
        {
            indexAngle = 0;
        }
        if (middleAngle <= SERVO_DEADZONE)
        {
            middleAngle = 0;
        }
        if (ringAngle <= SERVO_DEADZONE)
        {
            ringAngle = 0;
        }
        if (pinkieAngle <= SERVO_DEADZONE)
        {
            pinkieAngle = 0;
        }
        */

        // Command servos
        thumbServo.write(180 - thumbAngle);
        indexServo.write(180 - indexAngle);
        middleServo.write(180 - middleAngle);
        ringServo.write(180 - ringAngle);
        pinkieServo.write(180 - pinkieAngle);
    }
}

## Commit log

2025-10-02 Add contribution entry for Eli Campos on Draft Schematic
2025-10-02 Create principal schematic
    [echo_hand.kicad_pcb, echo_hand.kicad_sch]
2025-10-03 Add joystick and controller buttons
    [echo_hand.kicad_sch]
2025-10-03 Add controller buttons to schematic pdf
2025-10-11 Update BOM.md with new item entry
2025-10-11 Add entry for Flex Sensor purchase on 10/11/2025
2025-10-25 Add EchoHand flex sensor firmware
2025-10-26 logging start for Setting up Arduino environment and starting work on Bluetooth Serial
2025-10-26 finished arduino setup and showed that bluetooth serial fails cause the board does support it XD
2025-10-26 current progresss with BLE trying out NIMBLE library
2025-10-27 Add conversion to finger angle
2025-10-27 Add new BOM entry for Vibration Motors and tools
2025-11-05 finished getting it to work with dad board
2025-11-05 connecting it to esp32
2025-11-14 Add joystick, buttons, and servo support
2025-11-15 started group work and switching bluetooth to serial port, + debugging
2025-11-15 changed over to serial for the prototype, will later take out the printing serial task
2025-11-16 Update debug print logic
2025-11-17 Add Openhaptics support for finger angle & grab
2025-11-17 Fix formatting in README for Servo Motor System section
2025-11-17 Add new entries to BOM.md for prototype parts
2025-11-18 Revise section titles and add vibration motors details
    Updated section titles and added details about vibration motors.
2025-12-01 Replace bandpass filter with hardware
    [config.h]
2025-12-01 Add contribution entry for Eli Campos on noise filtering
2026-01-20 Fix serial method path
    [main.cpp]
2026-01-22 Add calibration phase & better adc polling
2026-01-25 Add contribution for potentiometer circuit modification
2026-01-29 starting CAD stuff
2026-01-29 started CAD Design for fingers for buttons and joystick
2026-01-30 finished up initial ring for joystick
    [JoystickRingM1.f3d, JoystickRingM1.stl]
2026-01-30 started design for button holder
2026-01-30 yay I finish now short nap
    [Button Ring2.f3d]
2026-01-31 starting adjusting to button rig design
2026-01-31 Made new casing for buttons
    [Button rig 3.f3d, Button rig 3.stl]
2026-02-06 made initial design for joystick before it arrives
    [Joystick Rig pt3_.f3d, Joystick Rig pt3_.stl]
2026-02-06 fixed missing time slot
2026-02-14 starting print fro joystick prototype
2026-02-15 forgot to checkout when finished print and redisign
2026-02-18 Upload electronics case
    This was created by Thingiverse user ottosboy.
    [case_v2.stl, topcover_solid.stl]
2026-02-20 Add case design files
    [echohand_box_FINAL.FCStd]
2026-02-21 Add servo position reset upon startup
    [ServoControl_task.cpp, config.h, main.cpp]
2026-02-21 Fix Simulation, Test Soldered Circuit, and Fix Priority Bug
    [config.h]
2026-02-23 Add contribution entry for Eli Campos on servo delay
2026-02-24 step files
    [Button rig 3.step, Joystick Rig pt3_.step]
2026-02-24 Decrease servo delay
2026-03-03 Add contribution entry for debugging pinkie jitters
2026-03-03 Upload re-designed circuit case
    [echohand_box_FINAL.FCStd]
2026-03-03 Rename CAD files
    [EchoHand_circuit_case.FCStd, echohand_box_FINAL.FCStd]
2026-03-03 Update case version
    [EchoHand_circuit_case_v3.FCStd]
2026-03-03 Remove old case files
    [case_v2.stl, topcover_solid.stl]
2026-03-04 Start schematic capture
    [EchoHand_v2.kicad_pcb, EchoHand_v2.kicad_sch]
2026-03-04 Use extreme values for calibration not average
2026-03-04 Update contributions with Unity environment details
    Added contributions related to Unity environment setup and calibration changes.
2026-03-06 update contrib
    [Joystick Rig pt4_.f3d]
2026-03-26 Fix servo angle reset code on initialization
    [ServoControl_task.cpp]
2026-04-01 Change config for ADC1 only circuit
2026-04-06 Add esp32now wifi code for both devices
2026-04-20 Upload release candidate schematic
    [EchoHand_v2.kicad_sch, HC-05.step]
2026-04-20 Upload schematic PDF
2026-04-20 Make new case
    [EchoHand_circuit_case_v4.FCStd]
